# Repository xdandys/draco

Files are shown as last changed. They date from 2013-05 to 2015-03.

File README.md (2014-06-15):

Draco
==========

Draco is opensource HW&SW UAV flight controller board. It was primary designed for my needs, but anybody can manufacture it, use it or modify it. If you would like to own one, you can contact me. 

It has two MCUs on it. The smaller one is used for OSD. The bigger one is running [TauLabs][1] flight code.

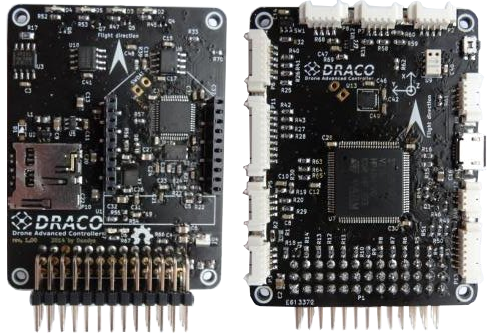
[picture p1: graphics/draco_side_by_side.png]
Draco board


###Features###
* main MCU STM32F4, MCU for OSD STM32F303CC
* 32MBit serial flash
* MPU9250 in SPI mode
* MS5611 in SPI mode
* CAN bus transceiver
* microSD slot via SDIO
* 4x A/D inputs
* slot for telemetry module (XBee or PirateBee)
* half-duplex inverted serial line for new FrSky S.PORT telemetry bus
* GPS port with power, UART and I2C for external compass
* 2x extension port with UART/I2C and GPIOs
* extension SPI port
* dedicated sonar port with power and trigger+echo signals
* microUSB
* 12x PWM in/out + 1x S.BUS/CPPM pin on 2.54mm header
* 6x LEDs
* micro button
* OSD with resolution 320x240, automatic PAL/NTSC detection
* dimmensions: 62x47mm

###TauLabs###
Draco is currently one of the non-official TauLabs target. You can find ported code at [my fork][2]. There are still some things missing and I will probably add them in short time:

* support for microSD card logging
* support of FrSky S.PORT telemetry protocol
* micro button support

  [1]: http://taulabs.org/
  [2]: https://github.com/strnadda/TauLabs/tree/draco

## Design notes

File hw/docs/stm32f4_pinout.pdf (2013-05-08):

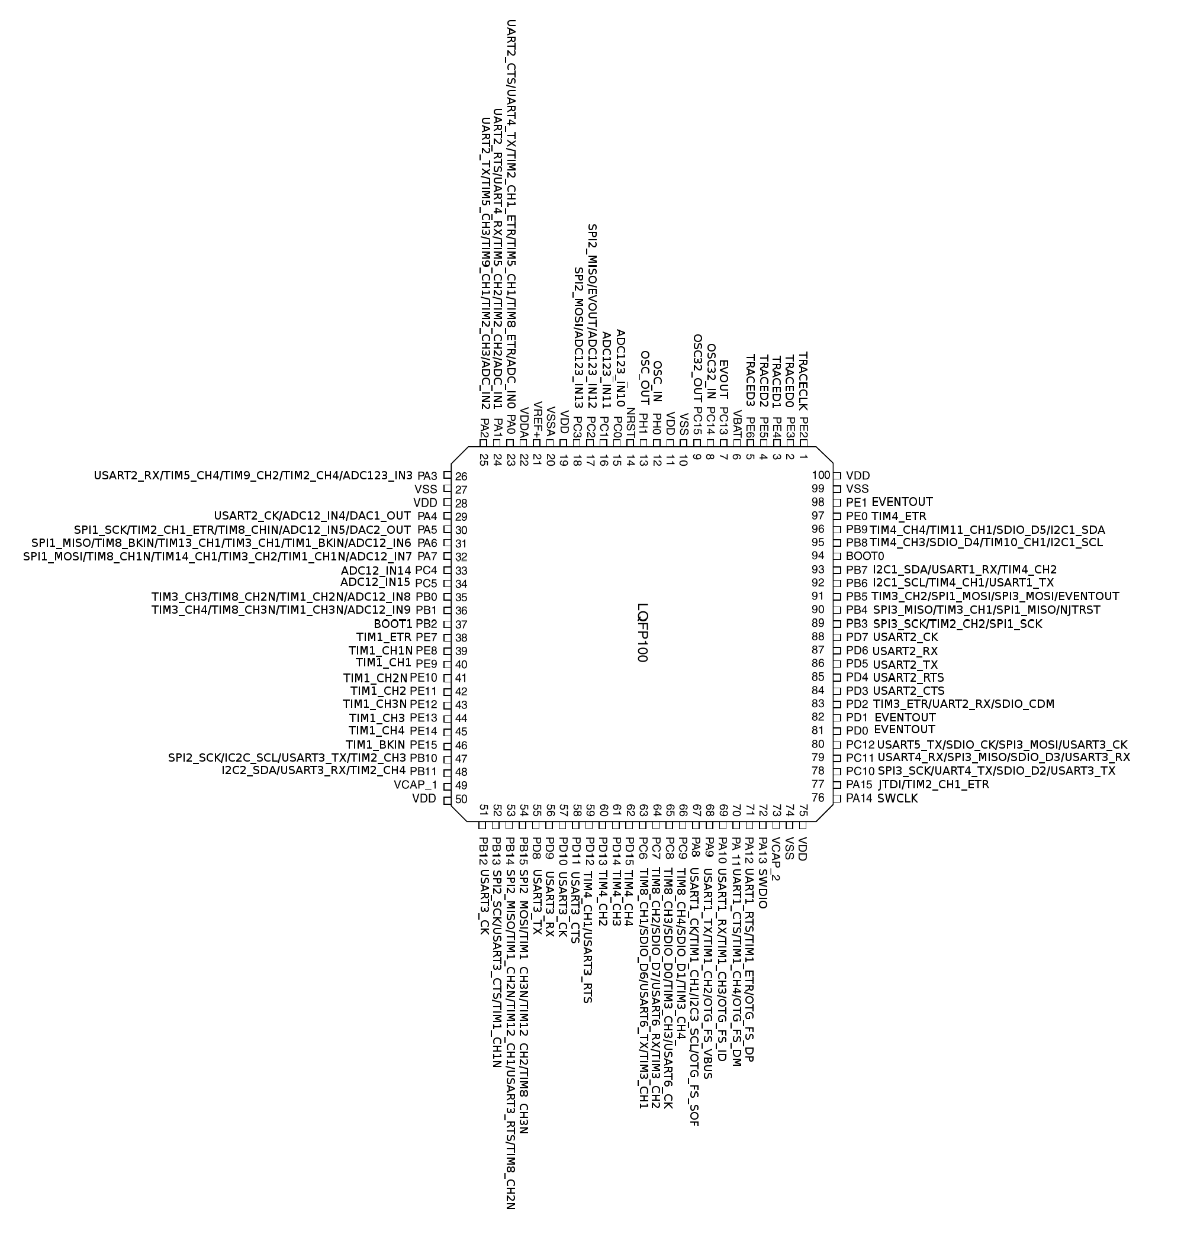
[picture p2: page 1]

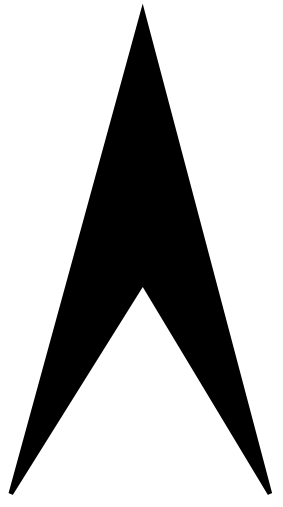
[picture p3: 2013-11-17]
hw/graphics/arrow.png

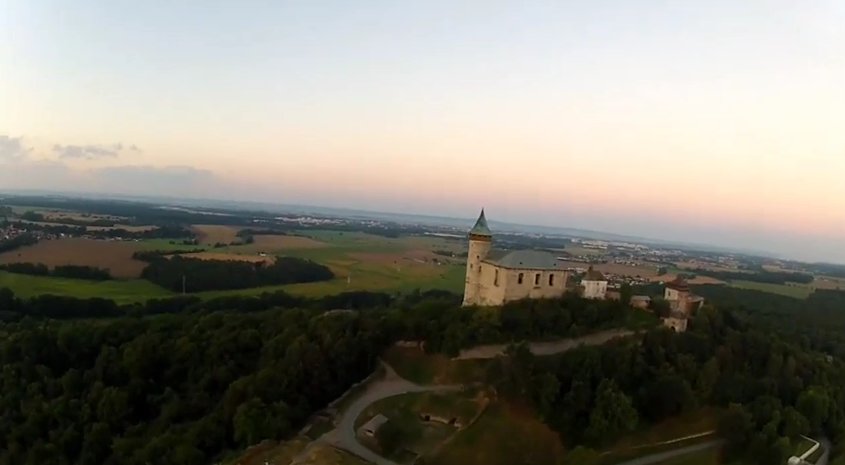
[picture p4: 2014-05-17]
fw/osdmcu/src/qtsim/qtosdsim/osd_back2.jpg

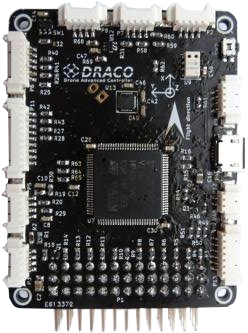
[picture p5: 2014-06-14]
graphics/draco_bottom.png

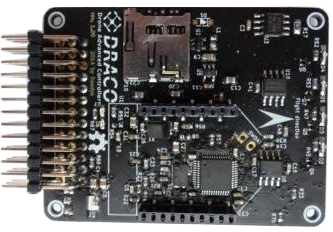
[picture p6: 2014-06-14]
graphics/draco_top_90deg.png

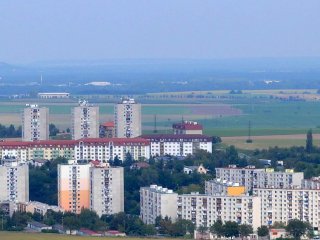
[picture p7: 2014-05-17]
fw/osdmcu/src/qtsim/qtosdsim/osd_back.jpg

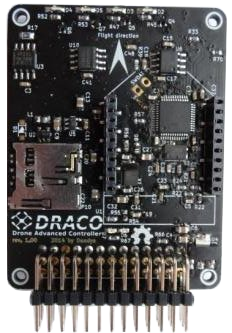
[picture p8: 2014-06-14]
graphics/draco_top.png

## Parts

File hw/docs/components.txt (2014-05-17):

---FINAL---
GPS: GMS-G9 (GPS + GLONASS + GALILEO, 10Hz, )
acc & gyro: MPU6000 (SPI mode)
mag: HMC5983 (SPI mode)
baro: MS5611 (SPI mode)
microSD slot: http://www.digikey.com/product-detail/en/101-00660-68-6/101-00660-68-6-1-ND/2187099?cur=USD
MCU: STM32F405VGT6
3.3V reg.: ADP3338AKCZ-3.3R (stabil_sot223_1)
shottky: PMEG3010BEA (sod323)
servo pin header: from hobbyking (pin_strip_10x3-90)
microUSB: http://www.digikey.com/product-detail/en/10104110-0001LF/609-4052-1-ND/2350358
NPN/PNP 100mA: PDTC114EE, PDTA114YE
crystal: http://www.digikey.com/product-detail/en/ABM3-8.000MHZ-D2Y-T/535-10630-1-ND/2344632
LED green: http://www.digikey.com/product-detail/en/APA2106ZGC/754-1062-1-ND/1747779
LED blue: http://www.digikey.com/product-detail/en/APA2106QBC%2FD/754-1425-1-ND/2163783
LED orange: http://www.digikey.com/product-detail/en/APA2106SECK/754-1059-1-ND/1747776
LED red: http://www.digikey.com/product-detail/en/APA2106SURCK/754-1060-1-ND/1747777
konektory xbee: http://www.digikey.com/product-search/en?vendor=0&keywords=S5901-10-ND

rozvaha na počet pinů:
MISO
MOSI
SCK
CS_HMC5983
CS_MPU6000
CS_MS5611
INT_MPU6000
LED1
LED2
LED3
PUSHBUTTON
SWCLK
SWDIO
PWM_1
PWM_2
PWM_3
PWM_4
PWM_5
PWM_6
PWM_7
PWM_8
PWM_9
PWM_10
PPM_INPUT
SDIO_D0
SDIO_D1
SDIO_D2
SDIO_D3
SDIO_CLK
XBEE_RX
XBEE_TX
XBEE_CTS
GPS_RX
GPX_TX
USB_DP
USB_DN
--EXT--
SONAR_TRIG
SONAR_ECHO
AD_INPUT_VOLTAGE
AD_CURRENT
AD_2
GPIO1
GPIO2
GPIO3
GPIO4
GPI2C_SDA
GPI2C_SCL
GPUART_TX
GPUART_RX

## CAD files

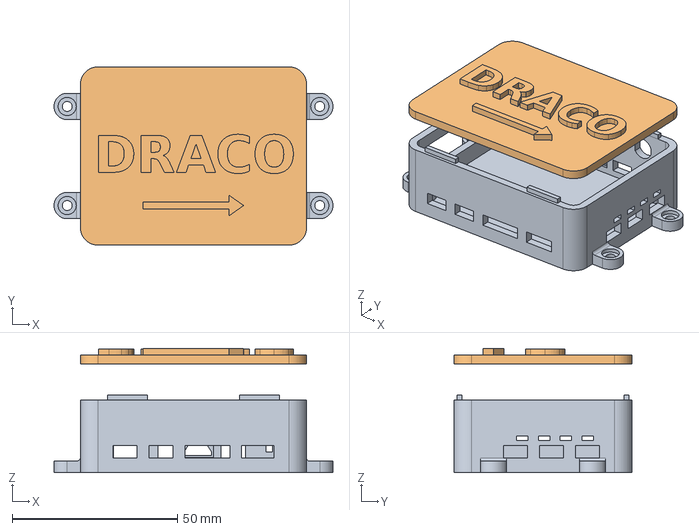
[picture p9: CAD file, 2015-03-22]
mech/draco.fcstd
84.5 x 54.0 x 37.7 mm
KRABICKA MultiTransform003
VICKO Pocket012

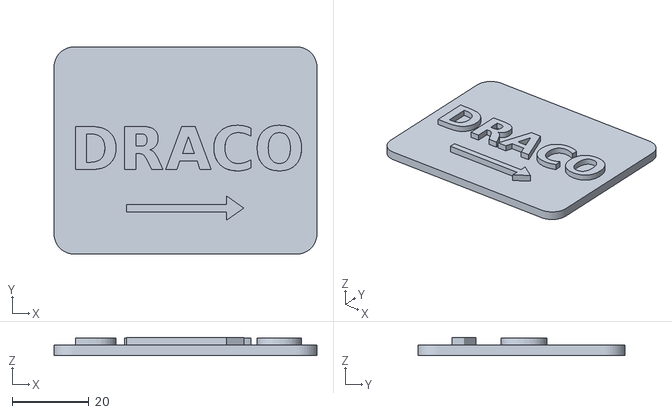
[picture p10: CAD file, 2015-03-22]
mech/lid.stl
68.5 x 54.0 x 4.70

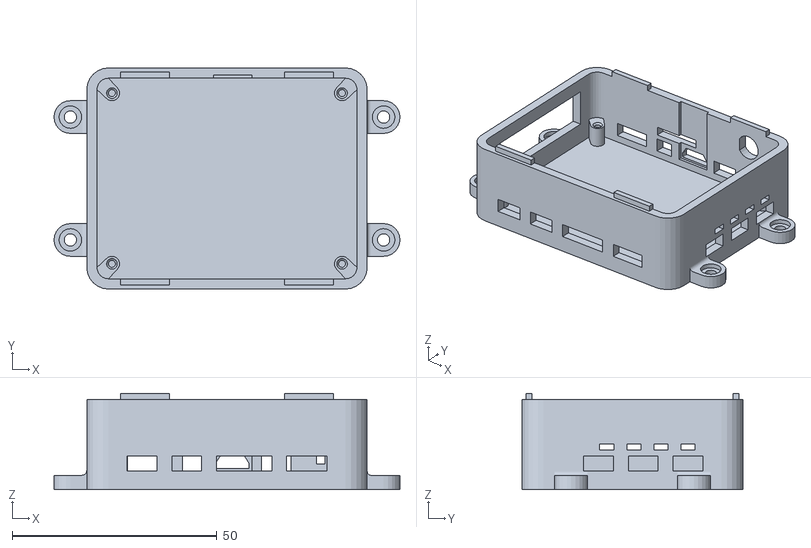
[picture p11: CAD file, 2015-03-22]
mech/box.stl
84.5 x 54.0 x 23.5

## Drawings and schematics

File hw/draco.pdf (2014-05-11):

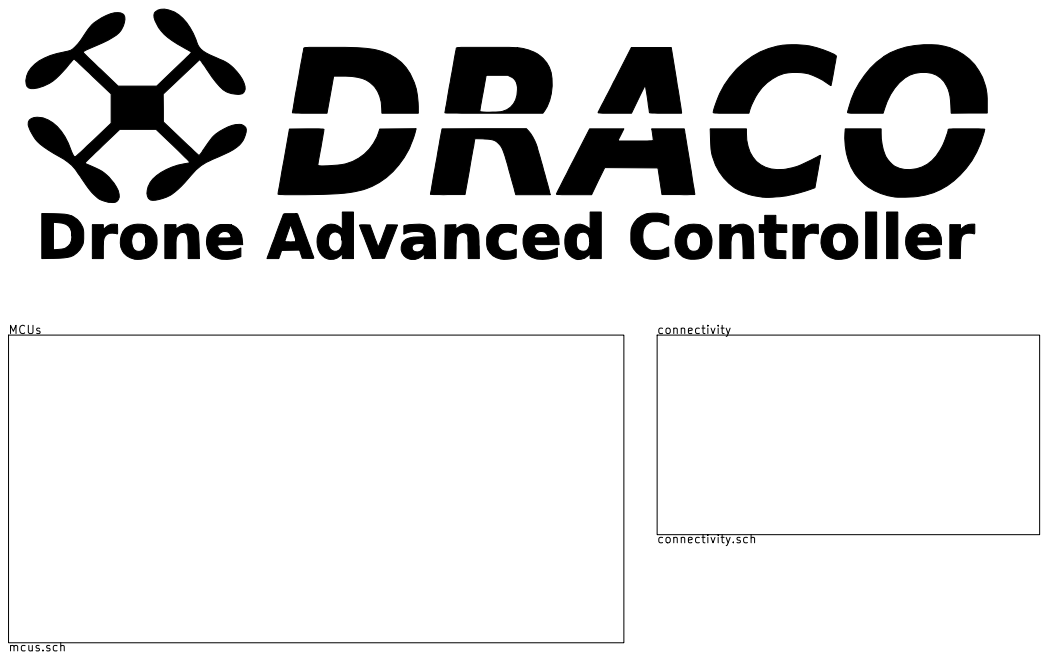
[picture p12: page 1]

connectivity.sch MCUs mcus.sch

dandys
Title: DRACO - Drone All in one Controller File: draco.sch Sheet: /

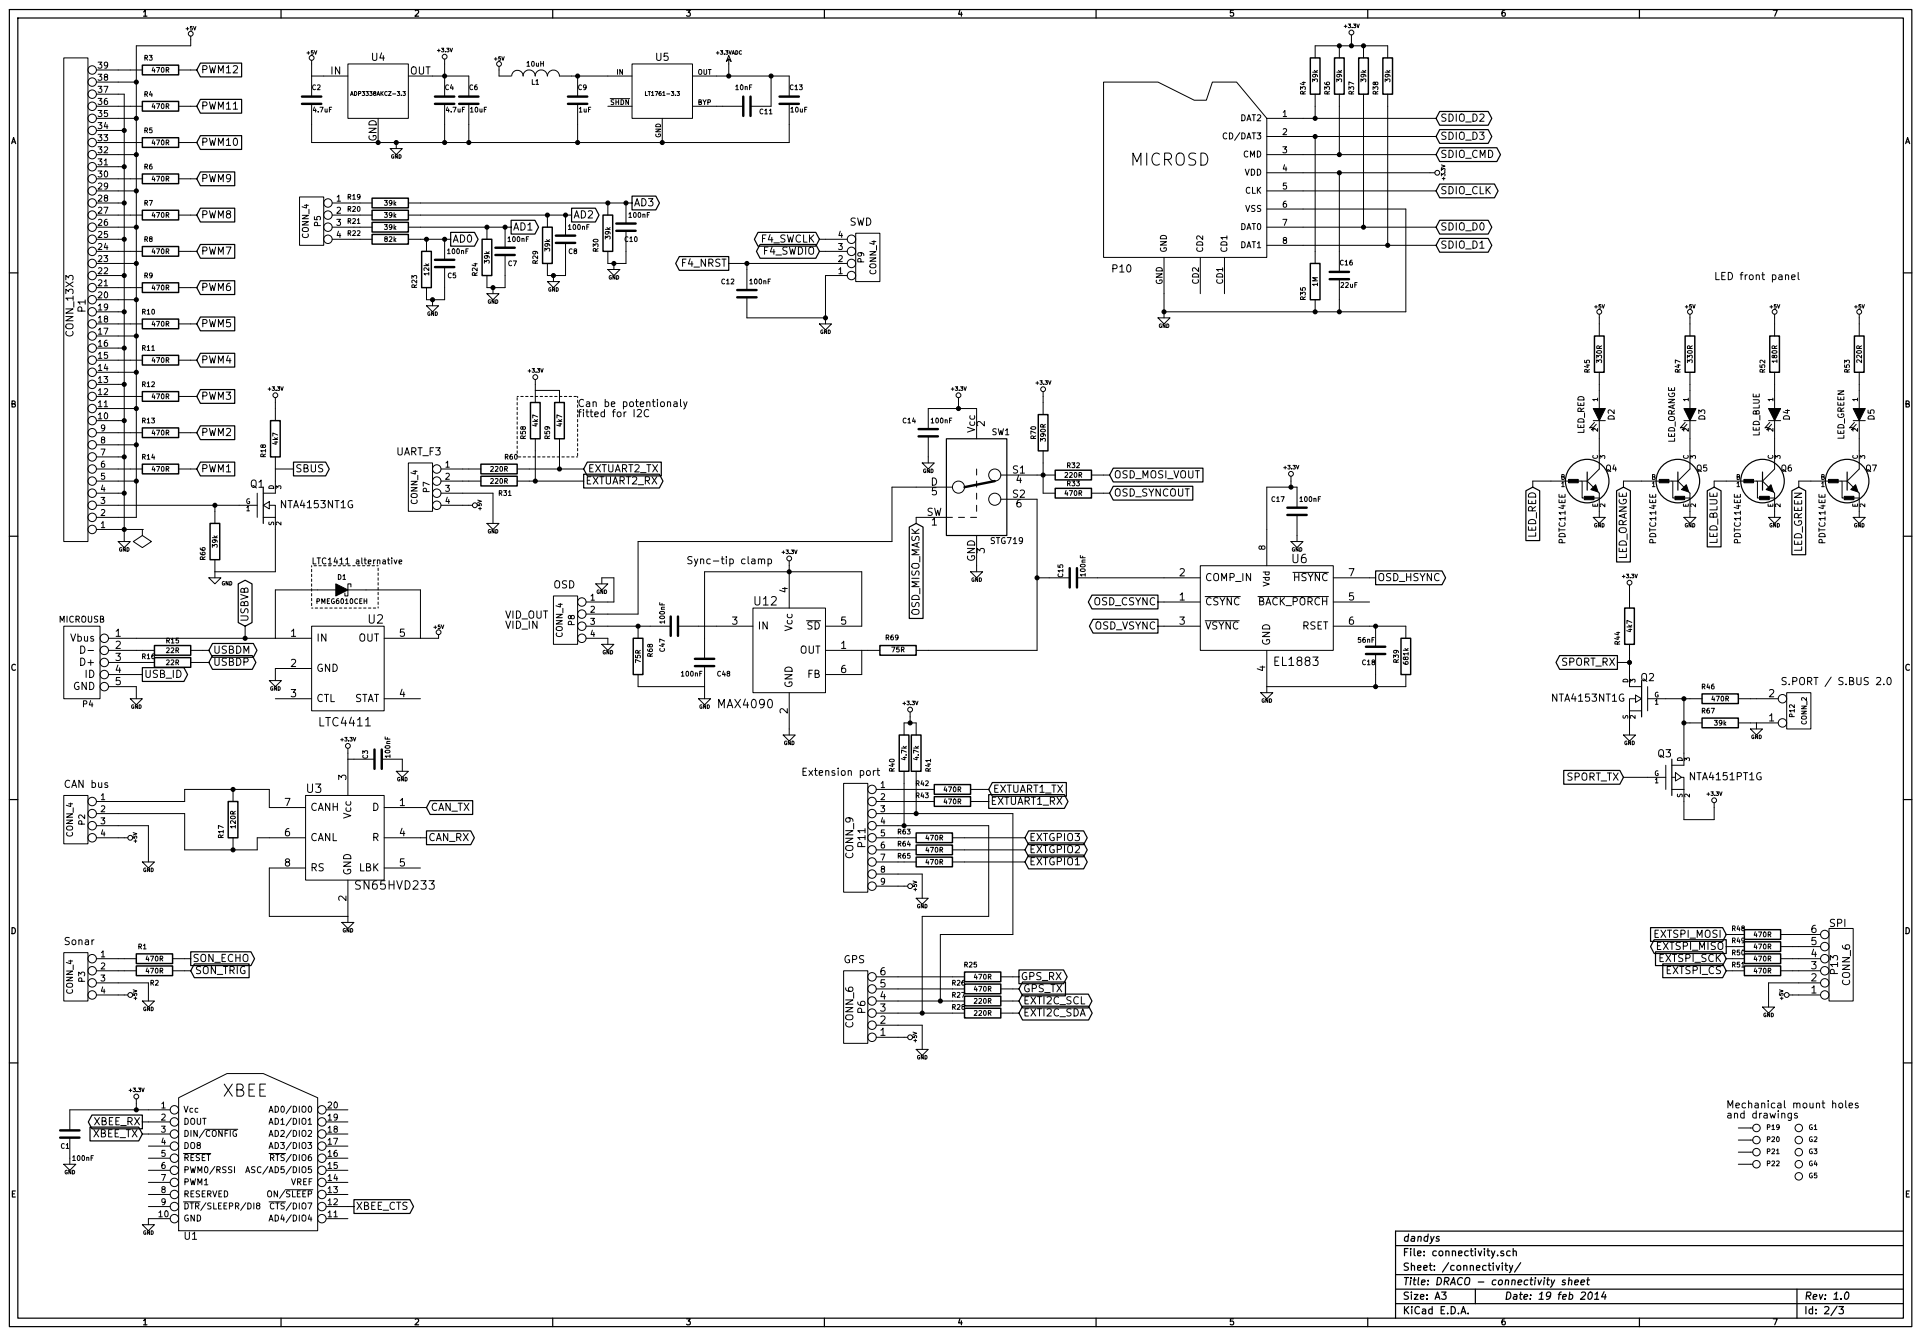
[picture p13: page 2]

P19 P20 P21 P22 Mechanical mount holes and drawings

dandys
File: connectivity.sch
Sheet: /connectivity/
Title: DRACO - connectivity sheet

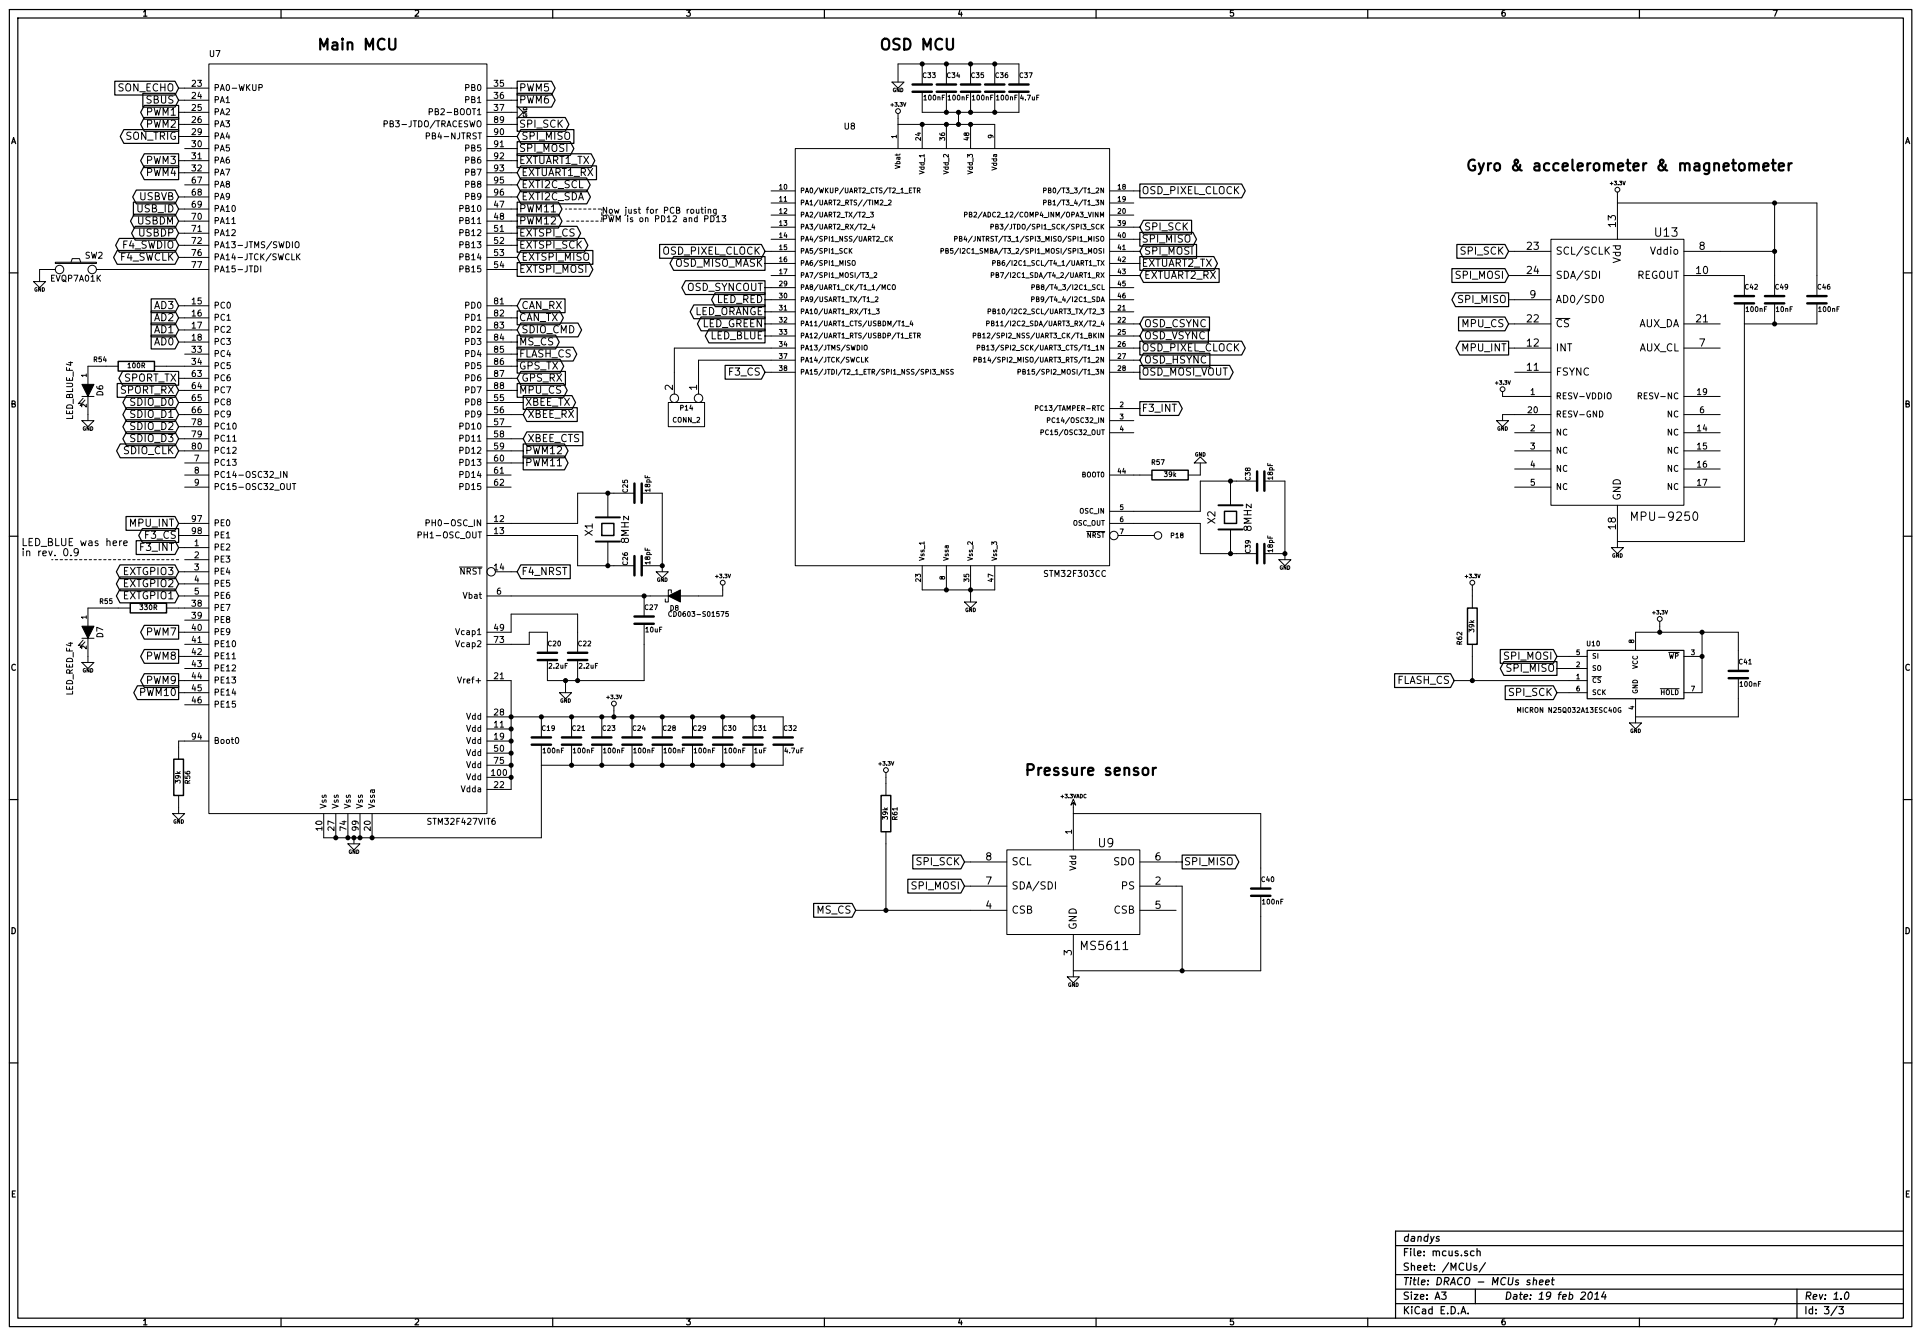
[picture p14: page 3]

9 PA0/WKUP/UART2_CTS/T2_1_ETR 10 PB2/ADC2_12/COMP4_INM/OPA3_VINM 20 PA9/USART1_TX/T1_2 30 PB4/JNTRST/T3_1/SPI3_MISO/SPI1_MISO 40 PA1/UART2_RTS//TIM2_2 11 PB10/I2C2_SCL/UART3_TX/T2_3 21 PA10/UART1_RX/T1_3 31 PB5/I2C1_SMBA/T3_2/SPI1_MOSI/SPI3_MOSI 41 PA2/UART2_TX/T2_3 12 PB11/I2C2_SDA/UART3_RX/T2_4 22 PA11/UART1_CTS/USBDM/T1_4 32 PB6/I2C1_SCL/T4_1/UART1_TX 42 PA3/UART2_RX/T2_4 13 Vss_1 23 PA12/UART1_RTS/USBDP/T1_ETR 33 PB7/I2C1_SDA/T4_2/UART1_RX 43 PA4/SPI1_NSS/UART2_CK 14 Vdd_1 24 PA13/JTMS/SWDIO 34 BOOT0 44 PA5/SPI1_SCK 15 PB12/SPI2_NSS/UART3_CK/T1_BKIN 25 Vss_2 35 PB8/T4_3/I2C1_SCL 45 PA6/SPI1_MISO 16 PB13/SPI2_SCK/UART3_CTS/T1_1N 26 Vdd_2 36 PB9/T4_4/I2C1_SDA 46 PA7/SPI1_MOSI/T3_2 17 PB14/SPI2_MISO/UART3_RTS/T1_2N 27 PA14/JTCK/SWCLK 37 Vss_3 47 PB0/T3_3/T1_2N 18 PB15/SPI2_MOSI/T1_3N 28 PA15/JTDI/T2_1_ETR/SPI1_NSS/SPI3_NSS 38 Vdd_3 48 PB1/T3_4/T1_3N 19 PA8/UART1_CK/T1_1/MCO 29 PB3/JTDO/SPI1_SCK/SPI3_SCK 39 U8 STM32F303CC

1 2 D7 LED_RED_F4 GND GND Pressure sensor

3 CSB 4 CSB 5 SDO 6 SDA/SDI 7 SCL 8 U9

Title: DRACO - MCUs sheet File: mcus.sch Sheet: /MCUs/

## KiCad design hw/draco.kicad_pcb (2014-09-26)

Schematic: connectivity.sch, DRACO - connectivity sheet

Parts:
C1, C3, C5, C7, C8, C10, C12, C14, C15, C17, C43, C47, C48: 100nF; c_0603
C2, C4: 4.7uF; c_0805
C6, C13: 10uF; c_0805
C9: 1uF; c_0805
C11: 10nF; c_0603
C16: 22uF; c_0805
C18: 56nF; c_0603
C44: 510pF; c_0603
D1: PMEG6010CEH
D2: LED_RED; led_2.1x0.6
D3: LED_ORANGE; led_2.1x0.6
D4: LED_BLUE; led_2.1x0.6
D5: LED_GREEN; led_2.1x0.6
D9: MBRS130T3G
D10: 1SMB7.0AT3G
G1, G2, G3, G4, G5: DUMMY
L1: 10uH; r_0805
P1: CONN_13X3; pin_strip_13x3-90
P2, P3, P5, P7, P8, P9: CONN_4; picoblade_4-90
P4: MICROUSB; conn_usb_B_micro_smd-FCI
P6, P13: CONN_6; picoblade_6-90
P10: MICROSD; MICRO-SD-SOCKET-PP
P11: CONN_9; picoblade_9-90
P12: CONN_2; picoblade_2-90
P19, P20, P21, P22: CONN_1; 1pin
Q2: NTA4153NT1G
Q3: NTA4151PT1G
Q4, Q5, Q6, Q7: PDTC114EE; sc75
R1, R2, R3, R4, R5, R6, R7, R8, R9, R10, R11, R12, R13, R14, R25, R26, R33, R42, R43, R46, R48, R49, R50, R51, R63, R64, R65: 470R; r_0603
R15, R16: 22R; r_0603
R17: 120R; r_0805
R18, R19, R20, R21, R24, R29, R30, R66, R67: 39k; r_0603
R22: 82k; r_0603
R23: 12k; r_0603
R27, R28, R31, R32, R53, R60: 220R; r_0603
R34, R36, R37, R38: 39k; r_0402
R35: 1M; r_0402
R39: 681k; r_0603
R40, R41: 4.7k; r_0603
R44, R58, R59: 4k7; r_0603
R45, R47: 330R; r_0603
R52: 180R; r_0603
R68, R69: 75R; r_0603
R70: 390R; r_0603
R71: 620R; r_0603
SW1: STG719; sot23-6
U1: XBEE; xbee-smt
U2: LTC4411; sot23-5
U3: SN65HVD233; so-8
U4: ADP3338AKCZ-3.3; stabil_sot223_1
U5: LT1761-3.3; tsot-5
U6: EL1883; so-8
U11: SN74AHC1G86
U12: MAX4090

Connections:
+3.3V: C1.2, C3.1, C4.1, C6.1, C14.2, C16.1, C17.2, C43.2, C48.1, P10.4, Q3.2 (S), R34.2, R36.2, R37.2, R38.2, R40.2, R41.2, R44.2, R58.2, R59.2, R70.2, SW1.2 (Vcc), U1.1, U3.3 (Vcc), U4.OUT, U6.8 (Vdd), U11.5 (Vcc), U12.4 (Vcc), U12.5 (~SD); also elsewhere on the board
+3.3VADC: C11.1, C13.1, U5.5 (OUT); also elsewhere on the board
+5V: D9.1 (A), P1.2, P1.5, P1.8, P1.11, P1.14, P1.17, P1.20, P1.23, P1.26, P1.29, P1.32, P1.35, P1.38, P2.4, P3.4, P6.1, P7.4, P11.9, P13.1, R45.2, R47.2, R52.2, R53.2
AD0: C5.2, R22.2, R23.2; also elsewhere on the board
AD1: C7.2, R21.2, R24.2; also elsewhere on the board
AD2: C8.2, R20.2, R29.2; also elsewhere on the board
AD3: C10.2, R19.2, R30.2; also elsewhere on the board
CAN_RX: U3.4 (R); also elsewhere on the board
CAN_TX: U3.1 (D); also elsewhere on the board
EXTGPIO1: R65.2; also elsewhere on the board
EXTGPIO2: R64.2; also elsewhere on the board
EXTGPIO3: R63.2; also elsewhere on the board
EXTI2C_SCL: R27.2; also elsewhere on the board
EXTI2C_SDA: R28.2; also elsewhere on the board
EXTSPI_CS: R51.1; also elsewhere on the board
EXTSPI_MISO: R49.1; also elsewhere on the board
EXTSPI_MOSI: R48.1; also elsewhere on the board
EXTSPI_SCK: R50.1; also elsewhere on the board
EXTUART1_RX: R43.2; also elsewhere on the board
EXTUART1_TX: R42.2; also elsewhere on the board
EXTUART2_RX: R31.2, R58.1; also elsewhere on the board
EXTUART2_TX: R59.1, R60.2; also elsewhere on the board
F4_NRST: C12.2, P9.2; also elsewhere on the board
F4_SWCLK: P9.4; also elsewhere on the board
F4_SWDIO: P9.3; also elsewhere on the board
GND: C1.1, C2.2, C3.2, C4.2, C5.1, C6.2, C7.1, C8.1, C9.2, C10.1, C12.1, C13.2, C14.1, C16.2, C17.1, C18.1, C43.1, C44.1, C48.2, D10.1 (A), P1.1, P1.4, P1.7, P1.10, P1.13, P1.16, P1.19, P1.22, P1.25, P1.28, P1.31, P1.34, P1.37, P2.3, P3.3, P4.5, P6.2, P7.3, P8.1, P8.4, P9.1, P10.6, P10.GND, P11.8, P12.1, P13.2, Q2.2 (S), Q4.2 (E), Q5.2 (E), Q6.2 (E), Q7.2 (E), R23.1, R24.1, R29.1, R30.1, R35.1, R39.1, R66.1, R67.2, R68.1, SW1.3 (GND), U1.10, U2.2 (GND), U3.2 (GND), U3.8 (RS), U4.GND, U5.2 (GND), U6.4 (GND), U11.3 (Gnd), U12.2 (GND); also elsewhere on the board
GPS_RX: R25.2; also elsewhere on the board
GPS_TX: R26.2; also elsewhere on the board
LED_BLUE: Q6.1 (B); also elsewhere on the board
LED_GREEN: Q7.1 (B); also elsewhere on the board
LED_ORANGE: Q5.1 (B); also elsewhere on the board
LED_RED: Q4.1 (B); also elsewhere on the board
unnamed: C47.1, U12.3 (IN)
unnamed: R69.2, U12.1 (OUT), U12.6 (FB)
unnamed: C47.2, P8.3, R68.2
unnamed: P11.6, R64.1
unnamed: P11.7, R65.1
unnamed: D5.2 (K), Q7.3 (C)
unnamed: P1.3, R66.2, U11.1 (IN1)
unnamed: C15.2, U6.2 (COMP_IN)
unnamed: C15.1, C44.2, R71.1
unnamed: P8.2, SW1.5 (D)
unnamed: R69.1, R71.2, SW1.6 (S2)
unnamed: C2.1, D1.2 (K), D9.2 (K), D10.2 (K), L1.1, U2.5 (OUT), U4.IN
unnamed: P11.1, R42.1
unnamed: P5.1, R19.1
unnamed: P11.5, R63.1
unnamed: P11.2, R43.1
unnamed: P5.3, R21.1
unnamed: P5.4, R22.1
unnamed: P5.2, R20.1
unnamed: C11.2, U5.4 (BYP)
unnamed: P6.6, R25.1
unnamed: P6.5, R26.1
unnamed: P6.3, P11.4, R28.1, R40.1
unnamed: D1.1 (A), P4.1, R18.2, U2.1 (IN)
unnamed: C9.1, L1.2, U5.1 (IN)
unnamed: P4.2, R15.1
unnamed: P4.3, R16.1
unnamed: P3.1, R1.1
unnamed: P3.2, R2.1
unnamed: P2.2, R17.1, U3.6 (CANL)
unnamed: P2.1, R17.2, U3.7 (CANH)
unnamed: P1.18, R10.1
unnamed: P1.15, R11.1
unnamed: P1.12, R12.1
unnamed: P1.6, R14.1
unnamed: P1.36, R4.1
unnamed: P1.33, R5.1
unnamed: P1.30, R6.1
unnamed: P13.3, R51.2
unnamed: P1.24, R8.1
unnamed: P1.27, R7.1
unnamed: P1.21, R9.1
unnamed: P7.1, R60.1
unnamed: C18.2, R39.2, U6.6 (RSET)
unnamed: P7.2, R31.1
unnamed: P1.39, R3.1
unnamed: P6.4, P11.3, R27.1, R41.1
unnamed: P1.9, R13.1
unnamed: Q2.1 (G), Q3.3 (D), R46.1, R67.1
unnamed: P12.2 (PM), R46.2
unnamed: P13.6, R48.2
unnamed: P13.5, R49.2
unnamed: P13.4, R50.2
unnamed: R32.1, R33.1, R70.1, SW1.4 (S1)
unnamed: D2.1 (A), R45.1
unnamed: D4.1 (A), R52.1
unnamed: D3.1 (A), R47.1
unnamed: D3.2 (K), Q5.3 (C)
unnamed: D4.2 (K), Q6.3 (C)
unnamed: D2.2 (K), Q4.3 (C)
unnamed: D5.1 (A), R53.1
OSD_HSYNC: U6.7 (~HSYNC~); also elsewhere on the board
OSD_MISO_MASK: SW1.1 (SW); also elsewhere on the board
OSD_MOSI_VOUT: R32.2; also elsewhere on the board
OSD_SYNCOUT: R33.2; also elsewhere on the board
OSD_VSYNC: U6.3 (~VSYNC~); also elsewhere on the board
PWM1: R14.2; also elsewhere on the board
PWM2: R13.2; also elsewhere on the board
PWM3: R12.2; also elsewhere on the board
PWM4: R11.2; also elsewhere on the board
PWM5: R10.2; also elsewhere on the board
PWM6: R9.2; also elsewhere on the board
PWM7: R8.2; also elsewhere on the board
PWM8: R7.2; also elsewhere on the board
PWM9: R6.2; also elsewhere on the board
PWM10: R5.2; also elsewhere on the board
PWM11: R4.2; also elsewhere on the board
PWM12: R3.2; also elsewhere on the board
SBUS: U11.4 (OUT); also elsewhere on the board
SBUS_UART_INVERT: U11.2 (IN2); also elsewhere on the board
SDIO_CLK: P10.5; also elsewhere on the board
SDIO_CMD: P10.3, R36.1; also elsewhere on the board
SDIO_D0: P10.7, R37.1; also elsewhere on the board
SDIO_D1: P10.8, R38.1; also elsewhere on the board
SDIO_D2: P10.1, R34.1; also elsewhere on the board
SDIO_D3: P10.2, R35.2; also elsewhere on the board
SON_ECHO: R1.2; also elsewhere on the board
SON_TRIG: R2.2; also elsewhere on the board
SPORT_RX: Q2.3 (D), R44.1; also elsewhere on the board
SPORT_TX: Q3.1 (G); also elsewhere on the board
USBDM: R15.2; also elsewhere on the board
USBDP: R16.2; also elsewhere on the board
USBVB: R18.1; also elsewhere on the board
USB_ID: P4.4; also elsewhere on the board
XBEE_CTS: U1.12; also elsewhere on the board
XBEE_RX: U1.2; also elsewhere on the board
XBEE_TX: U1.3; also elsewhere on the board

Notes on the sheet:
Sonar
CAN bus
Extension port
GPS
SWD
S.PORT / S.BUS 2.0
SPI
LED front panel
OSD
VID_OUT VID_IN
UART_F3
Can be potentionaly fitted for I2C
Mechanical mount holes and drawings
Sync-tip clamp
LTC1411 alternative

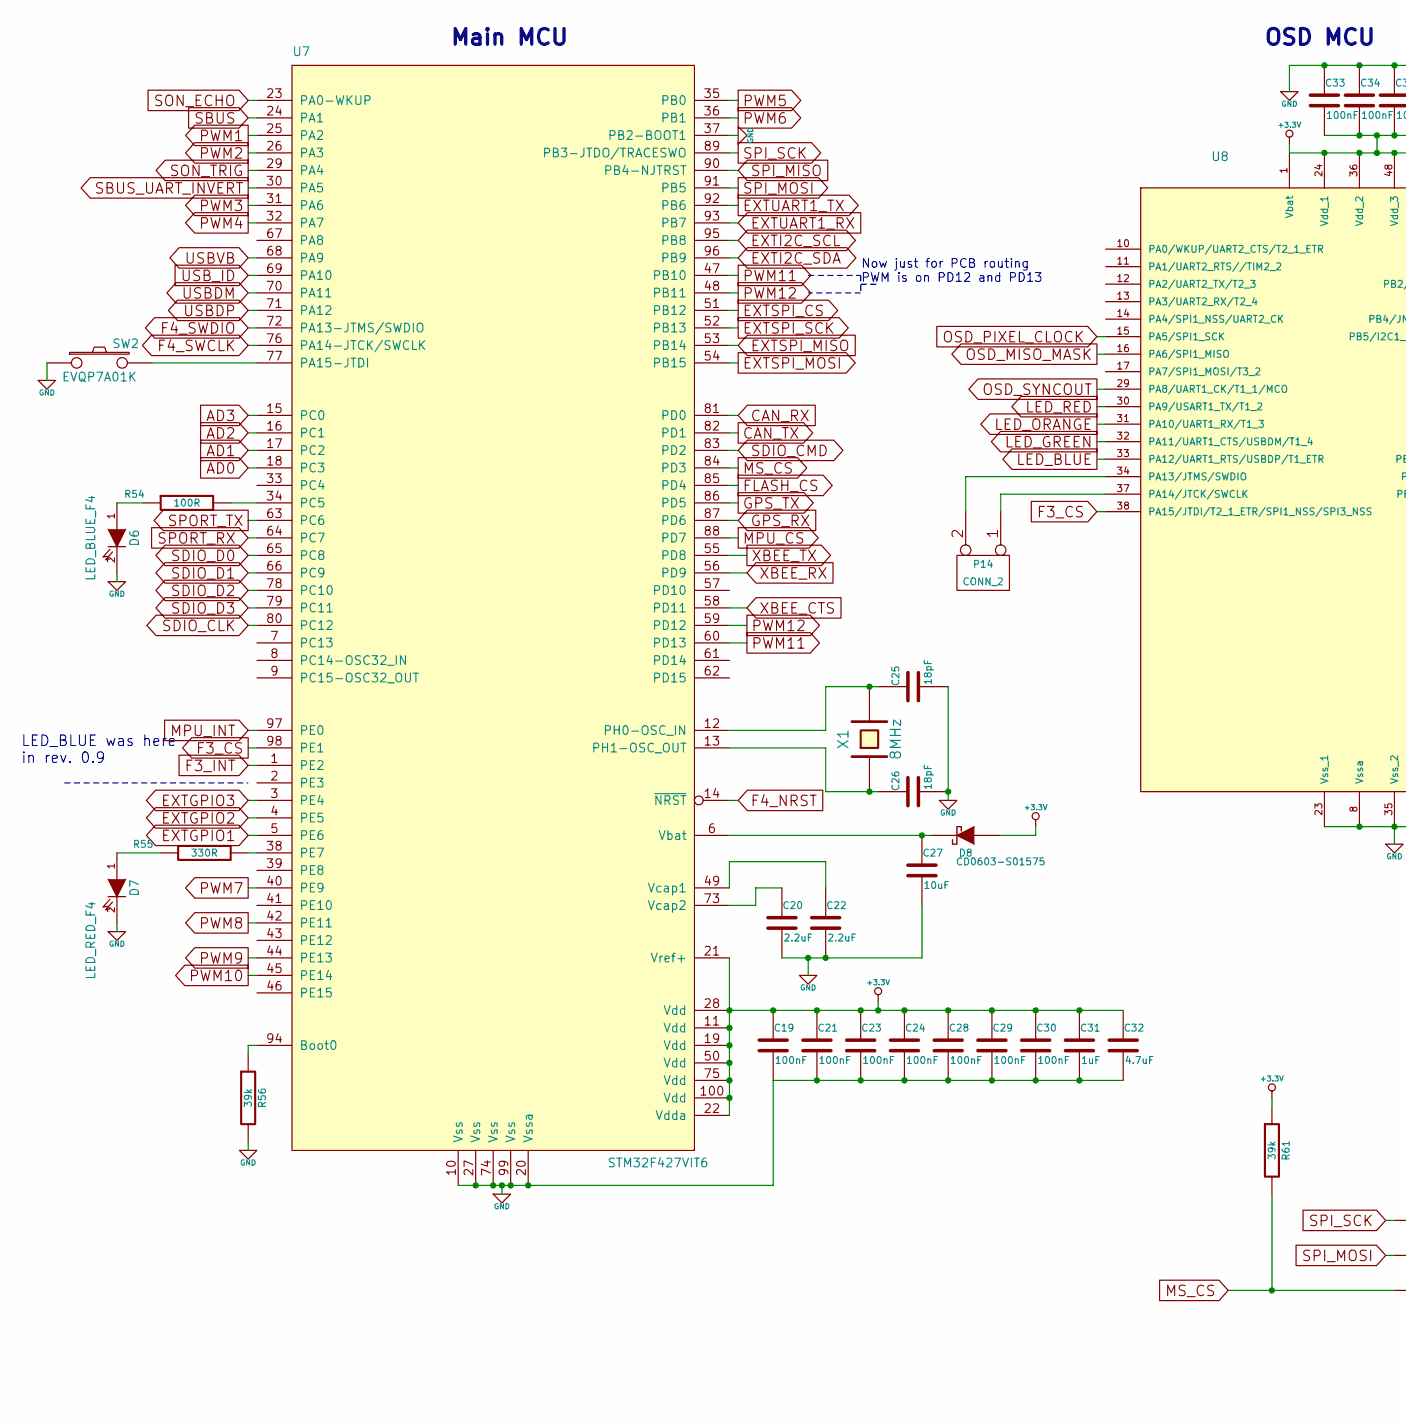
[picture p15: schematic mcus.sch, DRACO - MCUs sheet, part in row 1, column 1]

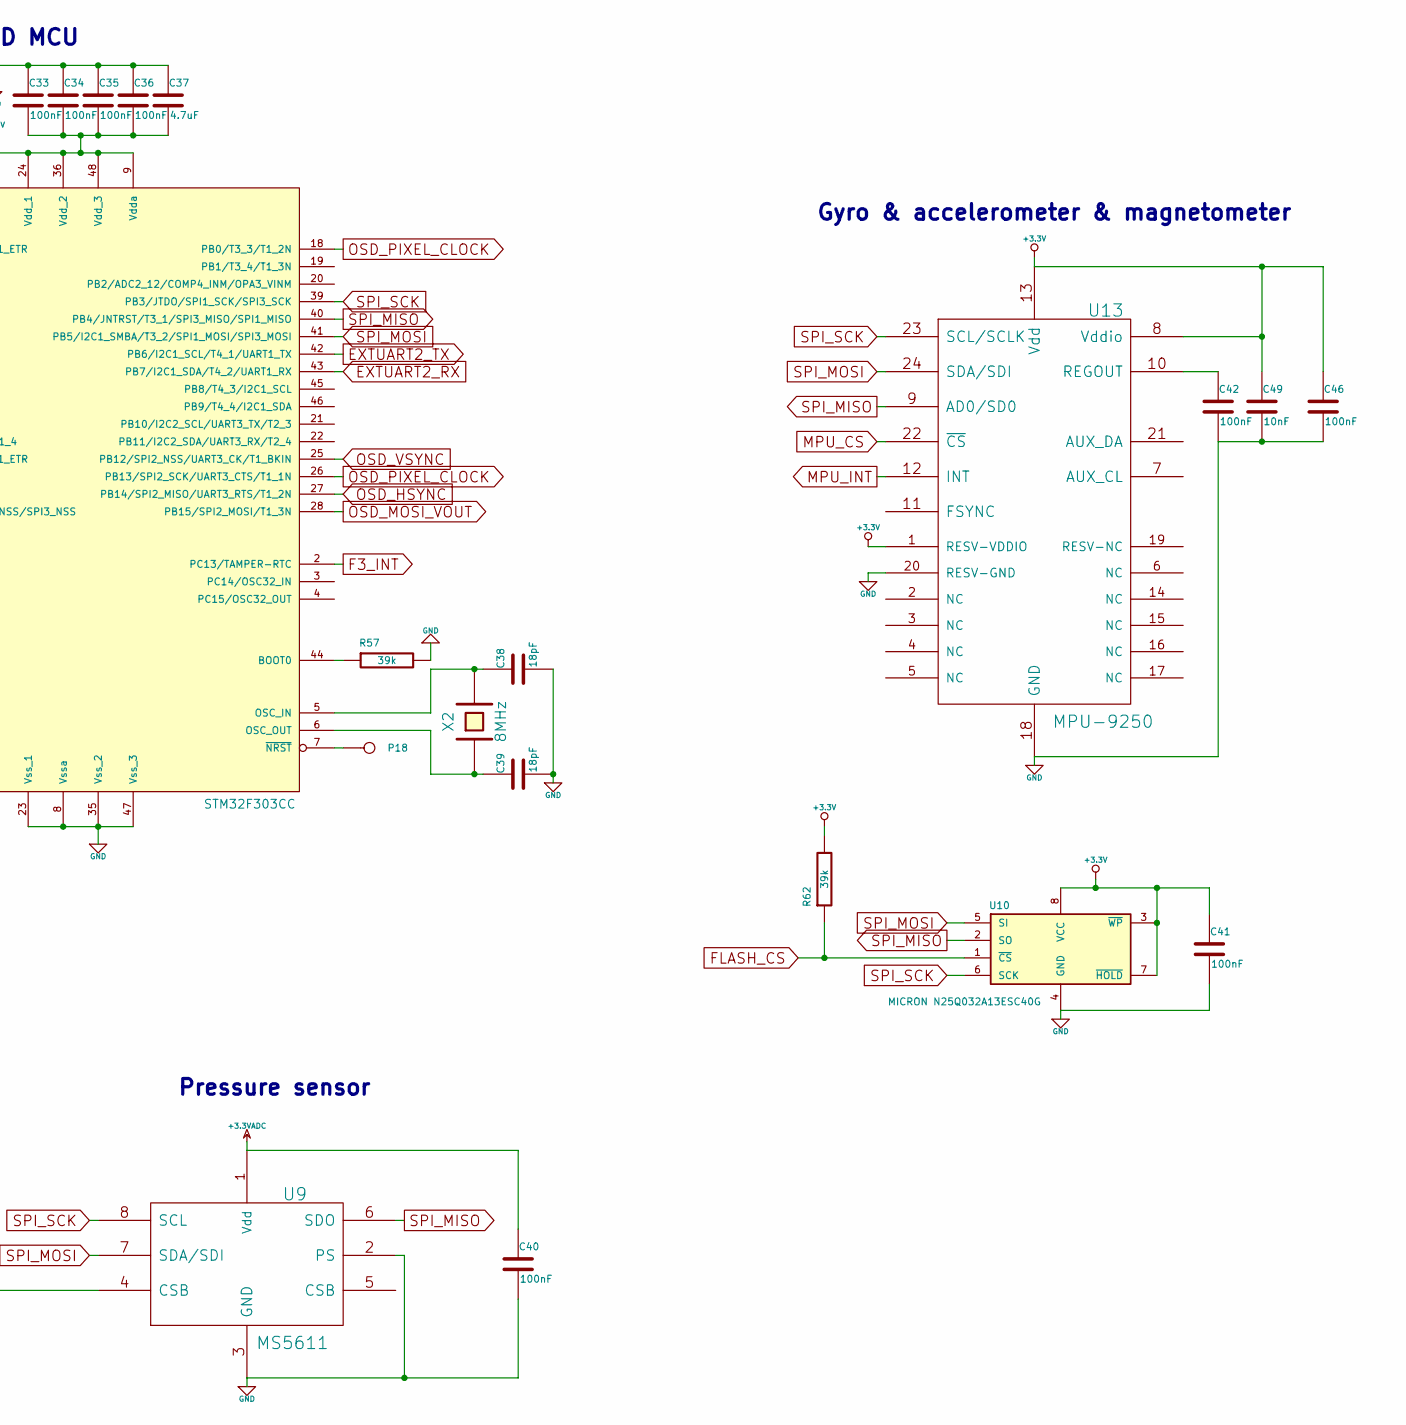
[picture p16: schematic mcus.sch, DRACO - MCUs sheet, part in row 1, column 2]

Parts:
C19, C21, C23, C24, C28, C29, C30, C33, C34, C35, C36, C40, C41, C42, C46: 100nF; c_0603
C20, C22: 2.2uF; c_0805
C25, C26, C38, C39: 18pF; c_0603
C27: 10uF; c_0805
C31: 1uF; c_0603
C32: 4.7uF; c_0805
C37: 4.7uF; c_0603
C49: 10nF; c_0603
D6: LED_BLUE_F4; Led_0603
D7: LED_RED_F4; Led_0603
D8: CD0603-S01575; r_0603
P14: CONN_2
P18: CONN_1; testpoint_pad
R54: 100R; r_0603
R55: 330R; r_0603
R56, R57, R61, R62: 39k; r_0603
SW2: EVQP7A01K
U7: STM32F427VIT6; TQFP-100
U8: STM32F303CC; lqfp48
U9: MS5611
U10: MICRON N25Q032A13ESC40G
U13: MPU-9250
X1, X2: 8MHz; crystal_smd_5x3.2mm

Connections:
+3.3V: C19.1, C21.1, C23.1, C24.1, C28.1, C29.1, C30.1, C31.1, C32.1, C33.2, C34.2, C35.2, C36.2, C37.2, C41.1, C46.1, C49.1, D8.1 (A), R61.1, R62.2, U7.11 (Vdd), U7.19 (Vdd), U7.21 (Vref+), U7.22 (Vdda), U7.28 (Vdd), U7.50 (Vdd), U7.75 (Vdd), U7.100 (Vdd), U8.1 (Vbat), U8.9 (Vdda), U8.24 (Vdd_1), U8.36 (Vdd_2), U8.48 (Vdd_3), U10.3 (~WP), U10.7 (~HOLD), U10.8 (VCC), U13.1 (RESV-VDDIO), U13.8 (Vddio), U13.13 (Vdd); also elsewhere on the board
+3.3VADC: C40.1, U9.1 (Vdd); also elsewhere on the board
AD0: U7.18 (PC3); also elsewhere on the board
AD1: U7.17 (PC2); also elsewhere on the board
AD2: U7.16 (PC1); also elsewhere on the board
AD3: U7.15 (PC0); also elsewhere on the board
CAN_RX: U7.81 (PD0); also elsewhere on the board
CAN_TX: U7.82 (PD1); also elsewhere on the board
EXTGPIO1: U7.5 (PE6); also elsewhere on the board
EXTGPIO2: U7.4 (PE5); also elsewhere on the board
EXTGPIO3: U7.3 (PE4); also elsewhere on the board
EXTI2C_SCL: U7.95 (PB8); also elsewhere on the board
EXTI2C_SDA: U7.96 (PB9); also elsewhere on the board
EXTSPI_CS: U7.51 (PB12); also elsewhere on the board
EXTSPI_MISO: U7.53 (PB14); also elsewhere on the board
EXTSPI_MOSI: U7.54 (PB15); also elsewhere on the board
EXTSPI_SCK: U7.52 (PB13); also elsewhere on the board
EXTUART1_RX: U7.93 (PB7); also elsewhere on the board
EXTUART1_TX: U7.92 (PB6); also elsewhere on the board
EXTUART2_RX: U8.43 (PB7/I2C1_SDA/T4_2/UART1_RX); also elsewhere on the board
EXTUART2_TX: U8.42 (PB6/I2C1_SCL/T4_1/UART1_TX); also elsewhere on the board
F3_CS: U7.98 (PE1), U8.38 (PA15/JTDI/T2_1_ETR/SPI1_NSS/SPI3_NSS)
F3_INT: U7.1 (PE2), U8.2 (PC13/TAMPER-RTC)
F4_NRST: U7.14 (~NRST~); also elsewhere on the board
F4_SWCLK: U7.76 (PA14-JTCK/SWCLK); also elsewhere on the board
F4_SWDIO: U7.72 (PA13-JTMS/SWDIO); also elsewhere on the board
FLASH_CS: R62.1, U7.85 (PD4), U10.1 (~CS)
GND: C19.2, C20.2, C21.2, C22.2, C23.2, C24.2, C25.2, C26.2, C27.2, C28.2, C29.2, C30.2, C31.2, C32.2, C33.1, C34.1, C35.1, C36.1, C37.1, C38.2, C39.2, C40.2, C41.2, C42.2, C46.2, C49.2, D6.2 (K), D7.2 (K), R56.2, R57.2, SW2.1, U7.10 (Vss), U7.20 (Vssa), U7.27 (Vss), U7.37 (PB2-BOOT1), U7.74 (Vss), U7.99 (Vss), U8.8 (Vssa), U8.23 (Vss_1), U8.35 (Vss_2), U8.47 (Vss_3), U9.2 (PS), U9.3 (GND), U10.4 (GND), U13.18 (GND), U13.20 (RESV-GND); also elsewhere on the board
GPS_RX: U7.87 (PD6); also elsewhere on the board
GPS_TX: U7.86 (PD5); also elsewhere on the board
LED_BLUE: U8.33 (PA12/UART1_RTS/USBDP/T1_ETR); also elsewhere on the board
LED_GREEN: U8.32 (PA11/UART1_CTS/USBDM/T1_4); also elsewhere on the board
LED_ORANGE: U8.31 (PA10/UART1_RX/T1_3); also elsewhere on the board
LED_RED: U8.30 (PA9/USART1_TX/T1_2); also elsewhere on the board
MPU_CS: U7.88 (PD7), U13.22 (~CS~)
MPU_INT: U7.97 (PE0), U13.12 (INT)
MS_CS: R61.2, U7.84 (PD3), U9.4 (CSB)
unnamed: C20.1, U7.73 (Vcap2)
unnamed: C22.1, U7.49 (Vcap1)
unnamed: C27.1, D8.2 (K), U7.6 (Vbat)
unnamed: R57.1, U8.44 (BOOT0)
unnamed: P18.1, U8.7 (~NRST~)
unnamed: R55.2, U7.38 (PE7)
unnamed: R56.1, U7.94 (Boot0)
unnamed: C42.1, U13.10 (REGOUT)
unnamed: D7.1 (A), R55.1
unnamed: R54.2, U7.34 (PC5)
unnamed: D6.1 (A), R54.1
unnamed: SW2.2, U7.77 (PA15-JTDI)
unnamed: P14.2 (PM), U8.34 (PA13/JTMS/SWDIO)
unnamed: P14.1, U8.37 (PA14/JTCK/SWCLK)
unnamed: C39.1, U8.6 (OSC_OUT), X2.1
unnamed: C38.1, U8.5 (OSC_IN), X2.2
unnamed: C25.1, U7.12 (PH0-OSC_IN), X1.2
unnamed: C26.1, U7.13 (PH1-OSC_OUT), X1.1
OSD_HSYNC: U8.27 (PB14/SPI2_MISO/UART3_RTS/T1_2N); also elsewhere on the board
OSD_MISO_MASK: U8.16 (PA6/SPI1_MISO); also elsewhere on the board
OSD_MOSI_VOUT: U8.28 (PB15/SPI2_MOSI/T1_3N); also elsewhere on the board
OSD_PIXEL_CLOCK: U8.15 (PA5/SPI1_SCK), U8.18 (PB0/T3_3/T1_2N), U8.26 (PB13/SPI2_SCK/UART3_CTS/T1_1N)
OSD_SYNCOUT: U8.29 (PA8/UART1_CK/T1_1/MCO); also elsewhere on the board
OSD_VSYNC: U8.25 (PB12/SPI2_NSS/UART3_CK/T1_BKIN); also elsewhere on the board
PWM1: U7.25 (PA2); also elsewhere on the board
PWM2: U7.26 (PA3); also elsewhere on the board
PWM3: U7.31 (PA6); also elsewhere on the board
PWM4: U7.32 (PA7); also elsewhere on the board
PWM5: U7.35 (PB0); also elsewhere on the board
PWM6: U7.36 (PB1); also elsewhere on the board
PWM7: U7.40 (PE9); also elsewhere on the board
PWM8: U7.42 (PE11); also elsewhere on the board
PWM9: U7.44 (PE13); also elsewhere on the board
PWM10: U7.45 (PE14); also elsewhere on the board
PWM11: U7.47 (PB10), U7.60 (PD13); also elsewhere on the board
PWM12: U7.48 (PB11), U7.59 (PD12); also elsewhere on the board
SBUS: U7.24 (PA1); also elsewhere on the board
SBUS_UART_INVERT: U7.30 (PA5); also elsewhere on the board
SDIO_CLK: U7.80 (PC12); also elsewhere on the board
SDIO_CMD: U7.83 (PD2); also elsewhere on the board
SDIO_D0: U7.65 (PC8); also elsewhere on the board
SDIO_D1: U7.66 (PC9); also elsewhere on the board
SDIO_D2: U7.78 (PC10); also elsewhere on the board
SDIO_D3: U7.79 (PC11); also elsewhere on the board
SON_ECHO: U7.23 (PA0-WKUP); also elsewhere on the board
SON_TRIG: U7.29 (PA4); also elsewhere on the board
SPI_MISO: U7.90 (PB4-NJTRST), U8.40 (PB4/JNTRST/T3_1/SPI3_MISO/SPI1_MISO), U9.6 (SDO), U10.2 (SO), U13.9 (AD0/SD0)
SPI_MOSI: U7.91 (PB5), U8.41 (PB5/I2C1_SMBA/T3_2/SPI1_MOSI/SPI3_MOSI), U9.7 (SDA/SDI), U10.5 (SI), U13.24 (SDA/SDI)
SPI_SCK: U7.89 (PB3-JTDO/TRACESWO), U8.39 (PB3/JTDO/SPI1_SCK/SPI3_SCK), U9.8 (SCL), U10.6 (SCK), U13.23 (SCL/SCLK)
SPORT_RX: U7.64 (PC7); also elsewhere on the board
SPORT_TX: U7.63 (PC6); also elsewhere on the board
USBDM: U7.70 (PA11); also elsewhere on the board
USBDP: U7.71 (PA12); also elsewhere on the board
USBVB: U7.68 (PA9); also elsewhere on the board
USB_ID: U7.69 (PA10); also elsewhere on the board
XBEE_CTS: U7.58 (PD11); also elsewhere on the board
XBEE_RX: U7.56 (PD9); also elsewhere on the board
XBEE_TX: U7.55 (PD8); also elsewhere on the board

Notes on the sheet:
Pressure sensor
Gyro & accelerometer & magnetometer
OSD MCU
Main MCU
Now just for PCB routing PWM is on PD12 and PD13
LED_BLUE was here in rev. 0.9

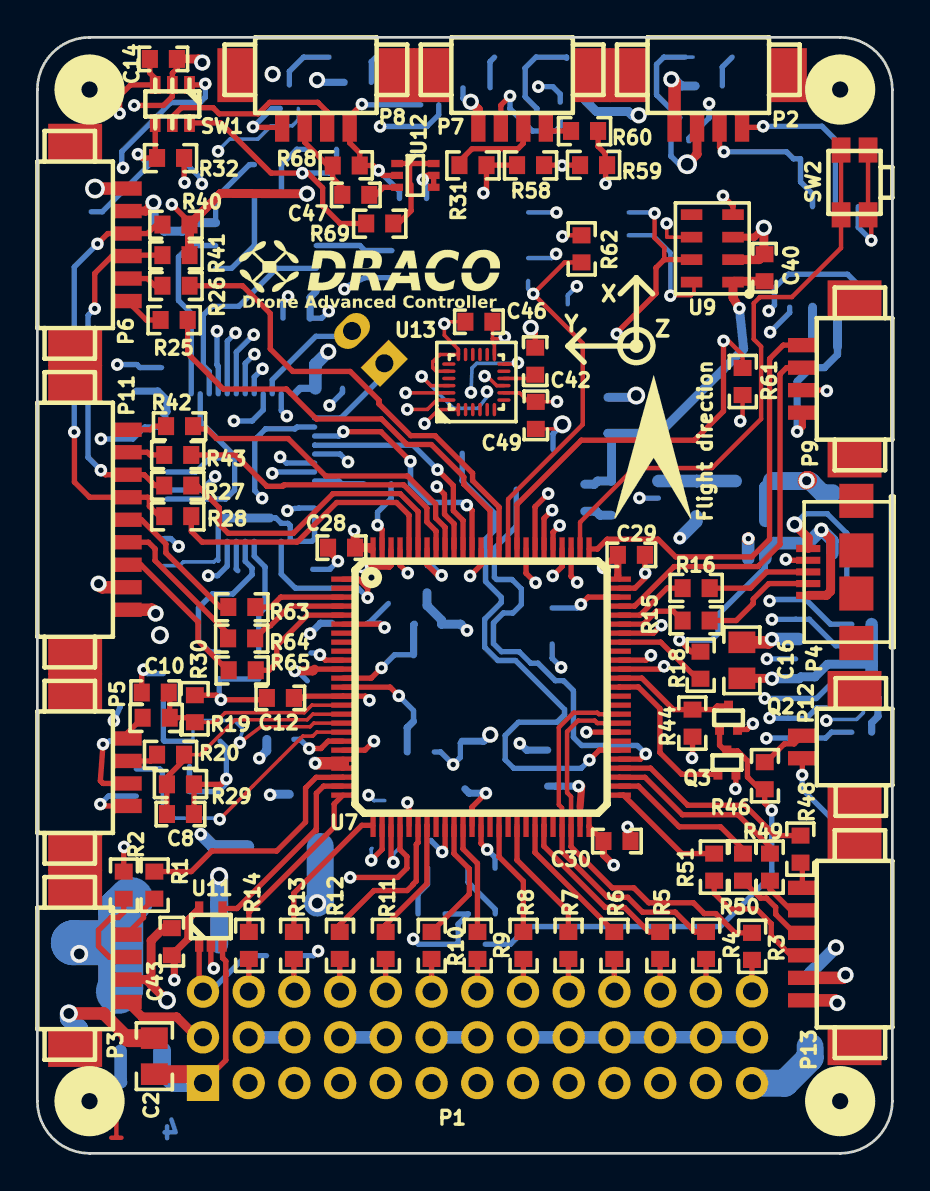
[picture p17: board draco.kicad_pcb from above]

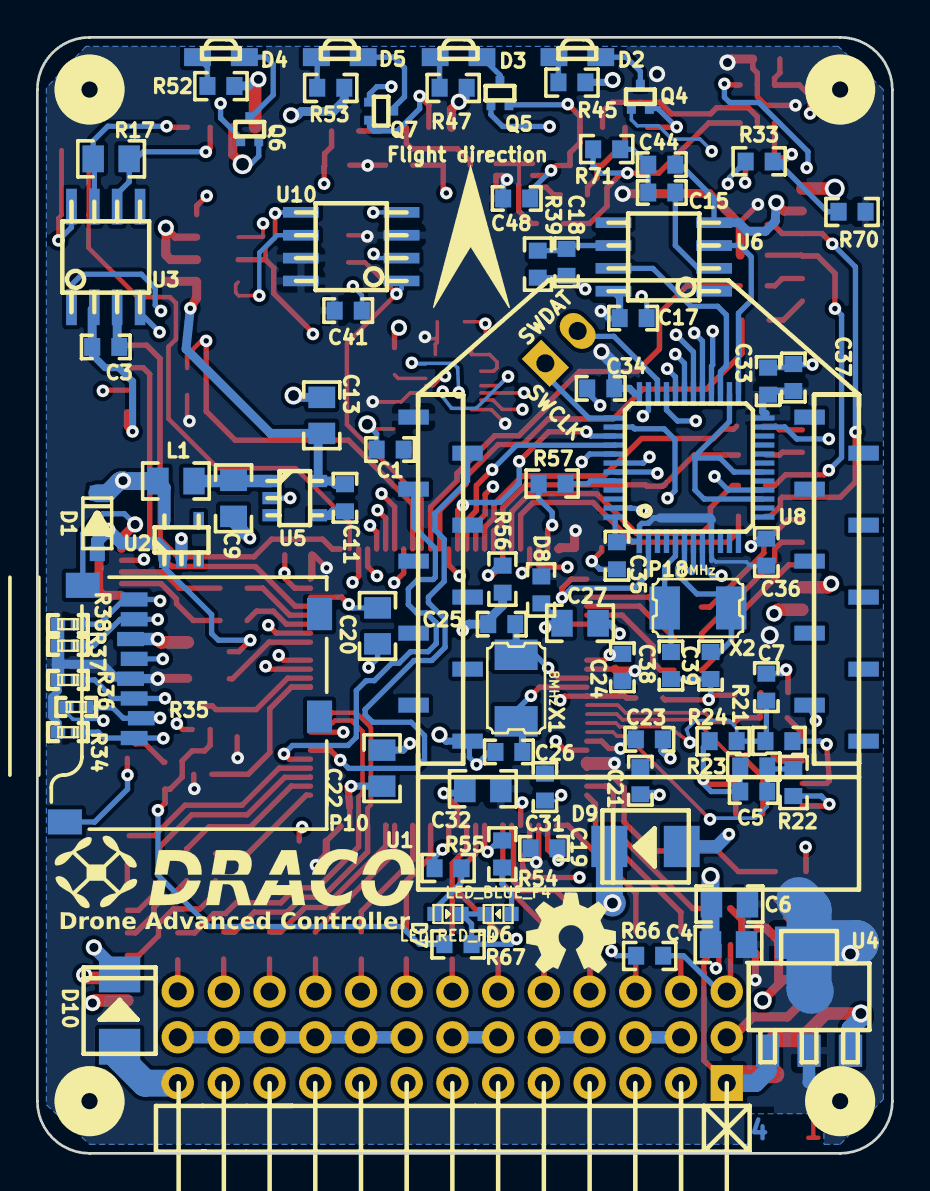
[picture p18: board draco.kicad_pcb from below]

Board: 4 copper layers, 47.5 x 62.0 mm, 177 parts (87 on the bottom side), 157 nets.

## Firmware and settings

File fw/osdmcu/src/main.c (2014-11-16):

/*
    DRACO - Copyright (C) 2013-2014 Daniel Strnad

    This file is part of DRACO project.

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
    You should have received a copy of the GNU General Public License
    along with this program.  If not, see <http://www.gnu.org/licenses/>.
*/
/**
 * @file    main.c
 * @brief   main()
 *
 */
#include "debug.h"
#include "delay.h"
#include "board.h"
#include "osdspi.h"
#include "led.h"
#include "delay.h"
#include "osdpainter.h"
#include "osdscreen.h"
#include "utils.h"
#include "comm.h"
#include "hud.h"
#include "swtimer.h"

int main(void)
{
    boardInit();
    sysTimerInit();
    ledInit();
    hudInit(&spiOsdDevice);
    commStart();
    while(1) {
        hudProcess();
        commProcess();
        swTimerProcess();
    }

    return 0;
}

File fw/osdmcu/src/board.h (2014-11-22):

/*
    DRACO - Copyright (C) 2013-2014 Daniel Strnad

    This file is part of DRACO project.

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
    You should have received a copy of the GNU General Public License
    along with this program.  If not, see <http://www.gnu.org/licenses/>.
*/
/**
 * @file    board.h
 * @brief   board specific defines goes here
 *
 */
#ifndef HW_H_
#define HW_H_

#define XTAL_FREQ       8000000UL
#define SYSCLK_FREQ     56000000UL

#include <stm32f30x.h>
#include <stm32f30x_rcc.h>
#include <stm32f30x_spi.h>
#include <stm32f30x_gpio.h>

#define VIDEO_BUFFER_MEM __attribute__ ((section(".videobuffer")))
#define DMA_MEM __attribute__ ((section(".dma")))

#define SPI_LEVEL                   SPI2
#define SPI_MASK                    SPI1
#define SPI_LEVEL_RCC_ENABLE        RCC->APB1ENR |= RCC_APB1ENR_SPI2EN;
#define SPI_LEVEL_RCC_DISABLE       RCC->APB1ENR &= ~RCC_APB1ENR_SPI2EN;
#define SPI_MASK_RCC_ENABLE         RCC->APB2ENR |= RCC_APB2ENR_SPI1EN;
#define SPI_MASK_RCC_DISABLE        RCC->APB2ENR &= ~RCC_APB2ENR_SPI1EN;
#define SPI_LEVEL_RCC_RESET         {RCC->APB1RSTR |= RCC_APB1RSTR_SPI2RST;RCC->APB1RSTR &= ~RCC_APB1RSTR_SPI2RST;}
#define SPI_MASK_RCC_RESET          {RCC->APB2RSTR |= RCC_APB2RSTR_SPI1RST;RCC->APB2RSTR &= ~RCC_APB2RSTR_SPI1RST;}
#define SPI_MASK_DMA                DMA1
#define SPI_LEVEL_DMA               DMA1
#define SPI_LEVEL_DMA_CH_TX         DMA1_Channel5
#define SPI_LEVEL_DMA_CH_TX_N       5
#define SPI_MASK_DMA_CH_TX          DMA1_Channel3
#define SPI_MASK_DMA_CH_TX_N        3
#define SPI_LEVEL_DMA_CH_IRQH       DMA1_Channel5_IRQHandler
#define SPI_MASK_DMA_CH_IRQH        DMA1_Channel3_IRQHandler
#define SPI_COMMIO                  SPI3
#define SPI_COMMIO_RCC_ENABLE       RCC->APB1ENR |= RCC_APB1ENR_SPI3EN
#define SPI_COMMIO_RCC_DISABLE      RCC->APB1ENR &= ~RCC_APB1ENR_SPI3EN;
#define SPI_COMMIO_RCC_RESET        {RCC->APB1RSTR |= RCC_APB1RSTR_SPI3RST;RCC->APB1RSTR &= ~RCC_APB1RSTR_SPI3RST;}
#define SPI_COMMIO_DMA              DMA2
#define SPI_COMMIO_DMA_CH_TX        DMA2_Channel2
#define SPI_COMMIO_DMA_CH_RX        DMA2_Channel1
#define SPI_COMMIO_DMA_CH_TX_N      2
#define SPI_COMMIO_DMA_CH_RX_N      1
#define SPI_COMMIO_DMA_CH_TX_IRQN   DMA2_Channel2_IRQn
#define SPI_COMMIO_DMA_CH_RX_IRQN   DMA2_Channel1_IRQn
#define SPI_COMMIO_IRQN             SPI3_IRQn
#define SPI_COMMIO_IRQ_GPIO         PinSpiInt
#define SPI_COMMIO_IRQ_HANDLER      SPI3_IRQHandler
#define SPI_COMMIO_DMA_IRQ_HANDLER  DMA2_Channel2_IRQHandler

typedef enum GPIOAliasEnum {

    PinOsdPixelClockIn,
    PinOsdMask,
    PinOsdSyncOut,
    PinLedRed,
    PinLedOrange,
    PinLedGreen,
    PinLedBlue,
    PinSpiCs,
    PinSpiSck,
    PinSpiMiso,
    PinSpiMosi,
    PinExtUart2Tx,
    PinExtUart2Rx,
    PinOsdCSync,
    PinOsdVSync,
    PinOsdPixelClockOut,
    PinOsdHSync,
    PinOsdVout,
    PinSpiInt,
    NoPin,
} GpioAlias;

void boardInit(void);
void jumpToBootLoader(uint16_t flags);

void gpioControl(GpioAlias alias, uint8_t on);
uint8_t gpioState(GpioAlias alias);
void gpioChangeMode(GpioAlias alias, GPIOMode_TypeDef mode);

void disableIrqs(void);
void enableIrqs(void);

void setupClocks(void);

#endif /* HW_H_ */

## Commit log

2013-11-17 Commited 0.9 rev
    [connectivity.sch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]
2014-01-26 Just cosmetic changes for eye-candy, no changes in board layout
    [connectivity.sch, draco.sch, mcus.sch]
2014-01-26 schematic: BJTs in S.BUS and S.PORT inverters replaced by MOSFETs (faster switching speed)
    [connectivity.sch, draco.sch, mcus.sch]
2014-02-11 Pixel clock (SPI SCK) connected to PB0 (TIM1) in schematic This will enable us to use both SPIs in slave mode with fine pixel clock tuning by timer TIM1
    [.kicad_pcb.kicad_pcb, connectivity.sch, draco.sch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]
2014-02-15 schematics: preparations for board rev. 1.0 MPU-6000 and HMC5893 replaced by single chip solution MPU-9250 Added video sync tip clamping MAX4090
    [connectivity.sch, draco.sch, mcus.sch]
2014-02-17 kicad libs: added walter w_switch library
2014-02-19 HW board revision 1.0
    - HMC5983 and MPU6000 replaced by MPU9250 on SPI bus
    - added video sync-tip clamping and buffer circuit MAX4090
    - added shottky diode D1 as optional alternative for ideal diode circuit LTC4411
    - SPI pixel clock generation now also connected to timer output for more fine clock tuning to be possible
    - PWM11 and PWM12 signals now switched to PD12 and PD13 to avoid collision of timer usage for sonar echo measurement
    - SMT32F4 LEDs moved to more suitable place on the board and blue LED switched to GPIO PC5 (was PE3)
    - added micro button
    - SWD pads for STM32F3 is now standard 2.54 pitch header
    - added SPI flash MICRON N25Q032A13ESC40G
    - added pulldown resistors for Q1, Q2
    [connectivity.sch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]
2014-05-11 Updated assembly csv and pdf schematic
    [draco.csv]
2014-05-17 Removed kicad backup file
    [.kicad_pcb.kicad_pcb]
2014-06-02 osdmcu: added SPI communication transport layer
2014-06-08 Polished OSD SPI driver and added PAL/NTSC autodetection
2014-06-08 spicomm: added SYNC frame
2014-06-08 fixed bug in GPS widget; updated gitignore
    [comm.c]
2014-06-09 spicomm: fixed processing of SYNC frame
    [spicomm.c]
2014-06-09 fix: prepare _next_ line in HSYNC interrupt
    [osdspi.c]
2014-06-14 added board images
2014-06-14 added another board image
2014-07-09 hud: allow attitude indicator to use whole horizontal screen resolution for pitch indication
2014-07-10 leds: fixed duty cycle calculation
    [led.c]
2014-09-24 hw: added diode from servo +5V to +3.3V stabs, TSV protection diode
    [connectivity.sch, draco.kicad_pcb, draco.sch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]
2014-09-24 hw: SBUS inverting FET replaced by XOR gate (controllable inverter)
    [connectivity.sch, draco.kicad_pcb, draco.sch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]
2014-09-25 hw: added series resistor to USB VBUS sense pin
    [connectivity.sch, draco.kicad_pcb, draco.sch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]
2014-09-25 hw: add chroma filter to sync separator, removed unused CSYNC signal
    [connectivity.sch, draco.kicad_pcb, mcus.sch]
2014-09-26 hw: rev 1.10, export for eurocircuits
    [draco-bot-cu.gbr, draco-bot-mask.gbr, draco-bot-silk.gbr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]
2014-10-27 hw: updated BOM for rev 1.10
    [draco.csv]
2014-11-16 style, white spaces and comments fix
    [board.c, board.h, comm.c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]
2014-11-19 hw: USB Vbus resistor value lowered to 18k
    [connectivity.sch, draco.sch, mcus.sch]
2014-11-23 bootloader: fixed time measuring issue with entering to bootloader, minor name changes
    [bootloader.c, comm.c, comm_commands.h]
2014-11-23 bootloader: fixed blockSize bug in chunkread
    [bootloader.c]
2015-03-22 mechanical: added printable 3D models for draco box
    [box.stl, draco.fcstd, lid.stl]
2015-07-18 added openocd flash script
    [oocdflash.cfg]

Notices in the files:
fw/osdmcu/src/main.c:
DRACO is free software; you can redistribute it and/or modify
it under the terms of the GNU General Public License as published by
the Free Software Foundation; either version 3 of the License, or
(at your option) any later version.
